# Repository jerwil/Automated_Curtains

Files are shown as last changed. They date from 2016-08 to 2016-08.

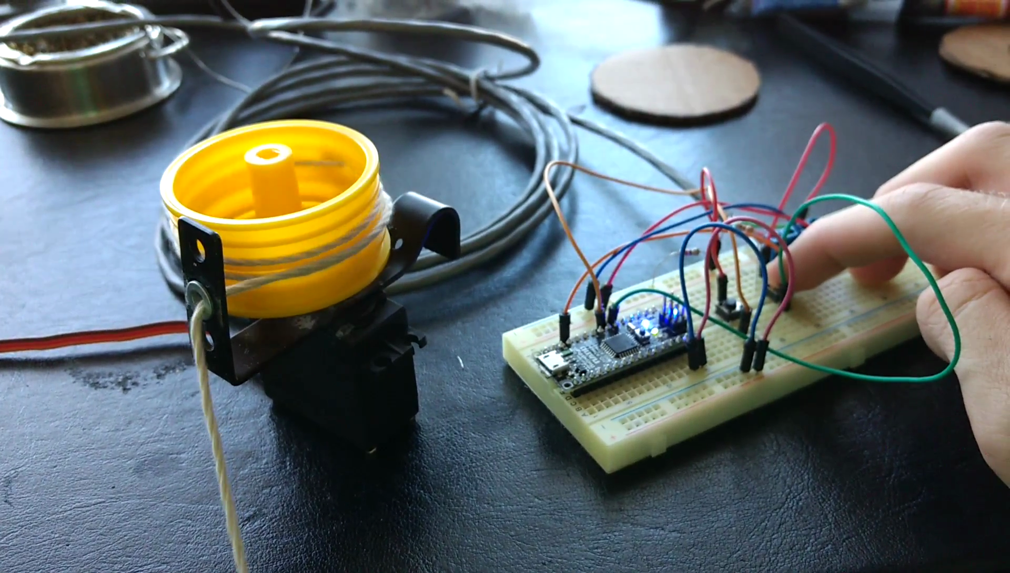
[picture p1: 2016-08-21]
Media/Progress Photos/Spool Test.png

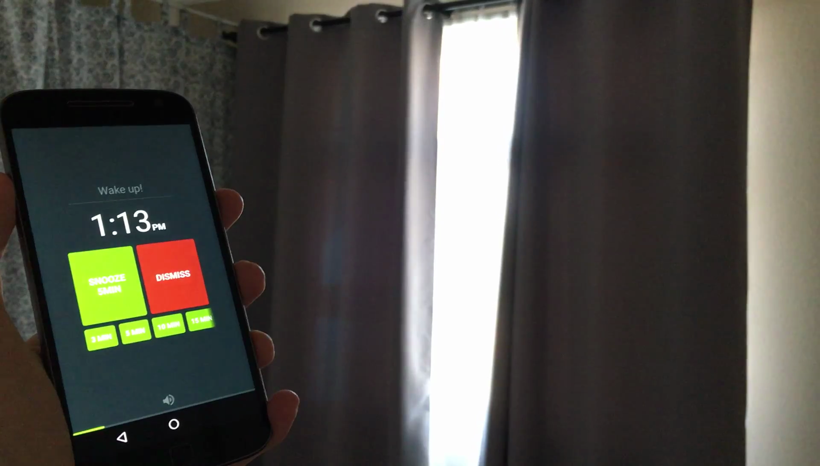
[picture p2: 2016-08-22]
Media/Curtain Opening.png

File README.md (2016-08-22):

# Alarm-Activated Automated Curtains
A system to automatically open the curtains when my cell phone alarm goes off

![] (https://github.com/jerwil/Automated_Curtains/raw/master/Media/Opening_GIF.gif)

##Features

* Uses inexpensive off-the-shelf parts to open curtain
* Seamlessly works with alarm app I already use
* Automatically retracts cord to allow curtains to be closed

##Architecture

![] (https://github.com/jerwil/Automated_Curtains/raw/master/Media/Comms%20Flowchart.png)

My alarm clock app, Sleep as Android, has the ability to interface with IFTTT. This is an awesome system that takes care of API calls for you and talks to hundreds of different services.

Sleep as Android >>> Adafruit IO

When the alarm goes off, Sleep as Android sends "alarm_alert_start" to a Maker channel feed. Using the [Sleep as Android documentation](http://sleep.urbandroid.org/documentation/integration/ifttt/), I created an [IFTTT recipe](https://ifttt.com/recipes/456351-when-my-sleep-as-android-alarm-goes-off-send-data-to-adafruit-io) that looks for this message, and writes a "1" to an Adafruit IO feed. When the alarm is disabled, "alarm_alert_dismiss" is sent, and a "0" is written to the data feed.

Adafruit IO >>> ESP8266

On the hardware side, I have an ESP8266 checking the Adafruit IO feed. I followed the basics of the [Adafruit guide](https://learn.adafruit.com/esp8266-temperature-slash-humidity-webserver/wiring) to get set up. When the feed returns a "1" the alarm is sounding, and the ESP8266 then lets the Arduino know it's time to open the curtain.

ESP8266 >>> Arduino

The connection between the ESP8266 and Arduino is very basic, just an on/off digital signal. When it's time to open the curtain, the ESP8266 writes a HIGH value on the digital line connecting the two microcontrollers.

Arduino Code

When the digital input is HIGH, the Arduino operates the servo to open the curtain, pauses, and then retracts the cord so that the curtain can be closed in the evening. The Arduino also has two buttons attached to it that allow the servo to be manually moved in either direction. These buttons also interrupt the automated open/close operation in case anything unexpected occurs.

The Arduino code also has a timeout (2 hours for now) during which no other alarm events will trigger the curtain opening. This avoids snoozing triggering the curtain multiple times in one morning.

## Wiring

![] (https://github.com/jerwil/Automated_Curtains/raw/master/Media/Breadboard%20Labeled.jpg)

See the included Fritzing diagram (.fzz file) for details. Thanks to [ydonnelly](https://github.com/ydonnelly/ESP8266_fritzing) for the ESP8266 Fritzing part!

![] (https://github.com/jerwil/Automated_Curtains/raw/master/Media/Breadboad.jpg)

## Hardware

![] (https://github.com/jerwil/Automated_Curtains/raw/master/Media/Servo%20Mounted.jpg)

The servo is mounted on the curtain rod, and has an old plastic wheel as a spool. As the servo turns, the spool reels in the string. The string is attached to the end of the curtain, so as it is pulled onto the spool, the curtain is dragged open.

![] (https://github.com/jerwil/Automated_Curtains/raw/master/Media/Progress%20Photos/Servo%20Washers.jpg)

The string has a bunch of washers along it such that there is tension when it unspools. The software will automatically unspool the string a few seconds after the curtain is dragged in so that the curtain can be later closed.

## Links

[Youtube video](https://www.youtube.com/watch?v=KcBI1g3s2vk)

[Hackaday.io Project Page](https://hackaday.io/project/13099-alarm-activated-curtains)

### License

<br /><span xmlns:dct="http://purl.org/dc/terms/" property="dct:title">Automated Curtains</span> by <a xmlns:cc="http://creativecommons.org/ns#" href="http://www.JeremyAdamWilson.com">Jeremy Wilson</a> is licensed under a <a rel="license" href="http://creativecommons.org/licenses/by-nc/4.0/">Creative Commons Attribution-NonCommercial 4.0 International License</a>.

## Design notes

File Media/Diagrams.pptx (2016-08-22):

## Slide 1

ESP8266

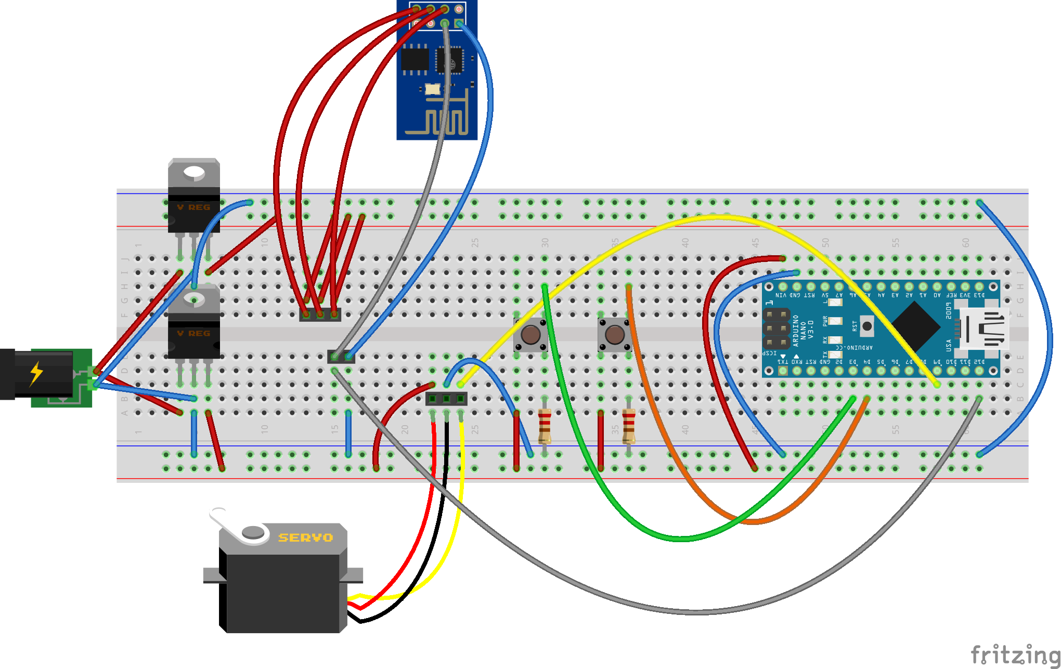
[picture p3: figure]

Manual open/close

3.3V

Arduino
Nano

5V

Alarm on/off signal

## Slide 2

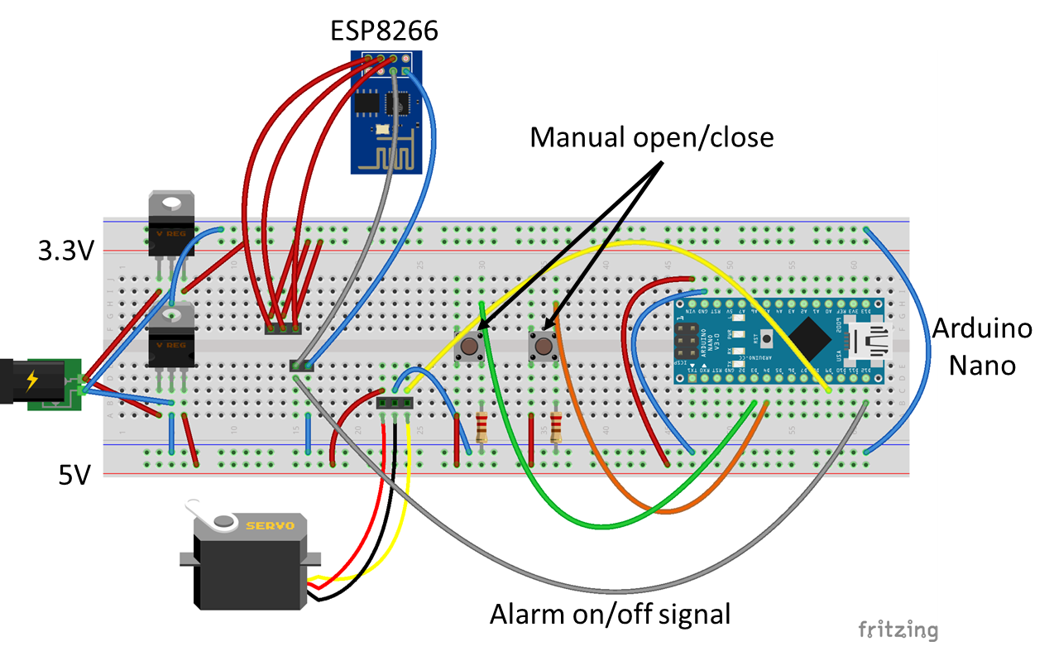
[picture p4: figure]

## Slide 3

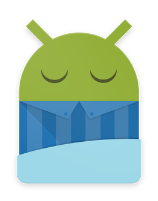
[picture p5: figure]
Screen Clipping

IFTTT Maker Channel

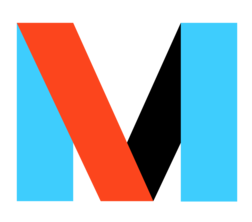
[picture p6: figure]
Screen Clipping

Adafruit IO

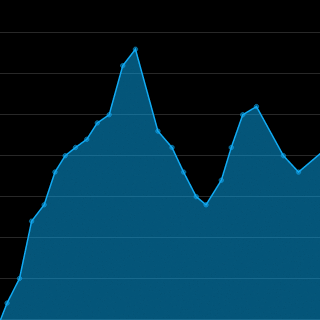
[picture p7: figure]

alarm_alert_start

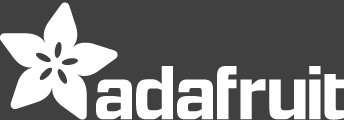
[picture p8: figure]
Adafruit Logo

Adafruit_IO_Client

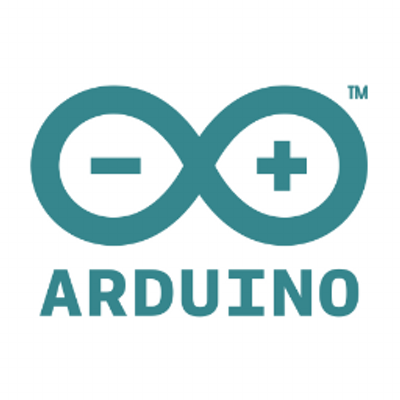
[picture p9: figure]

Servo

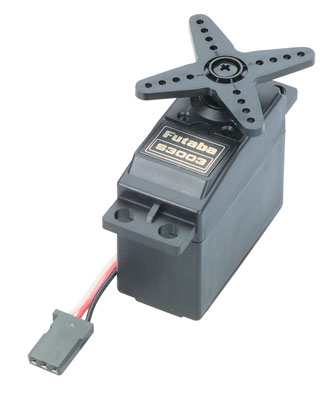
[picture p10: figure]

Nano

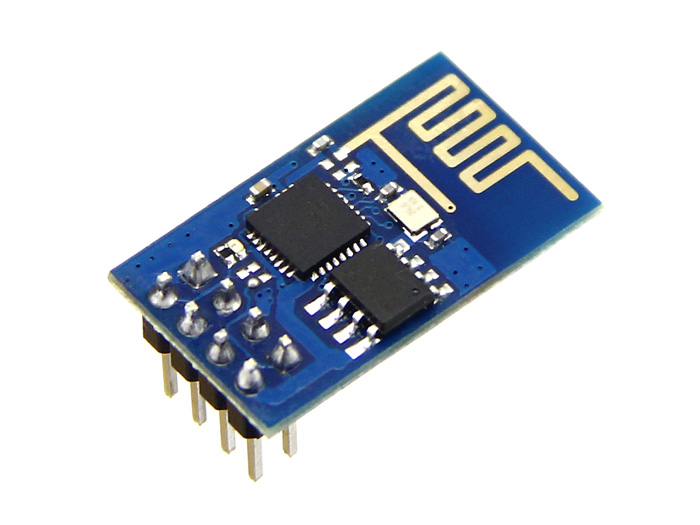
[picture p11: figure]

PWM

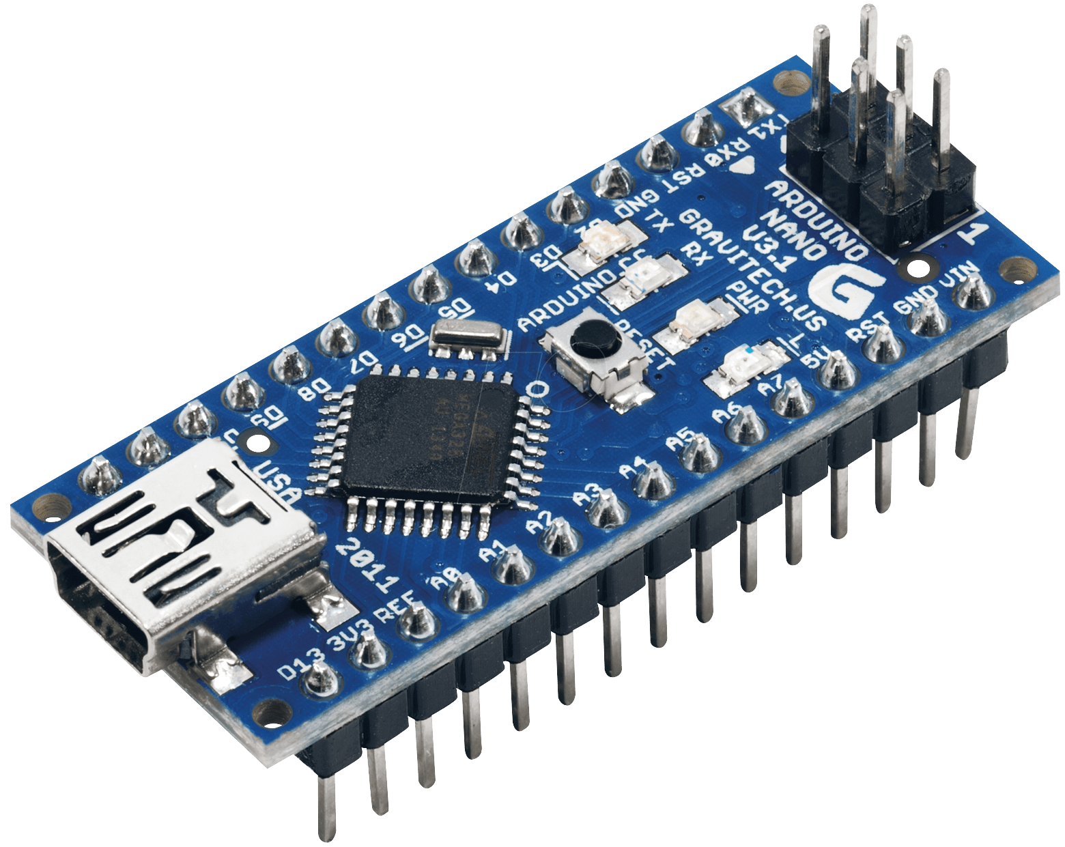
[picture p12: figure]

Digital HIGH

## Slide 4

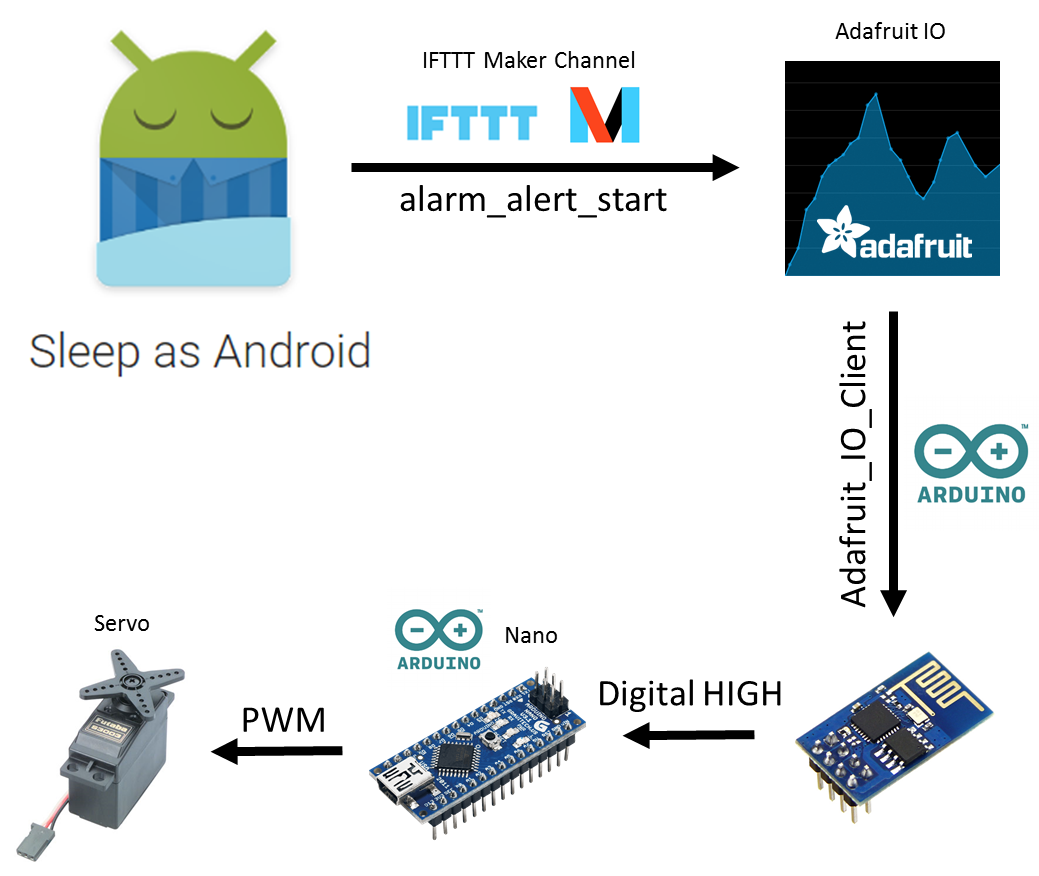
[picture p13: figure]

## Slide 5

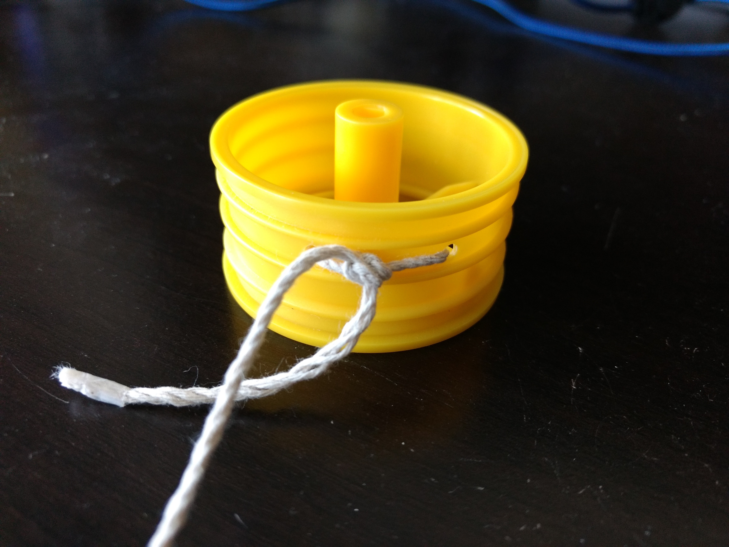
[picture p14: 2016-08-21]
Media/Progress Photos/Wheel as Spool.jpg

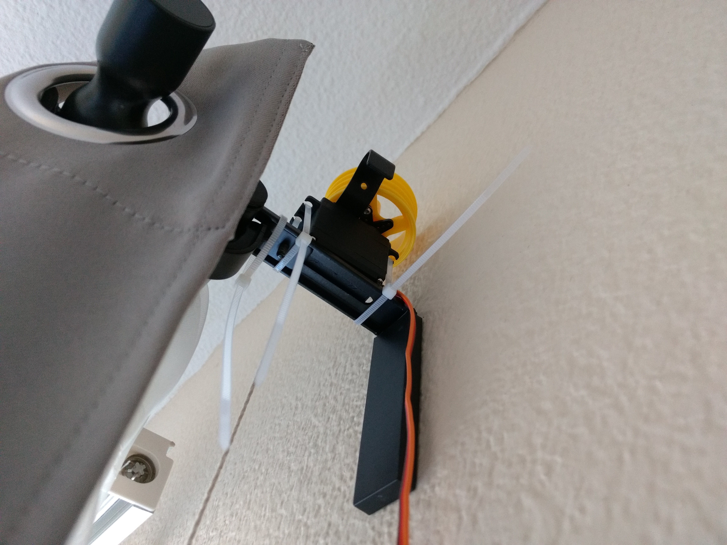
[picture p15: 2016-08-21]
Media/Progress Photos/Servo Mounted.jpg

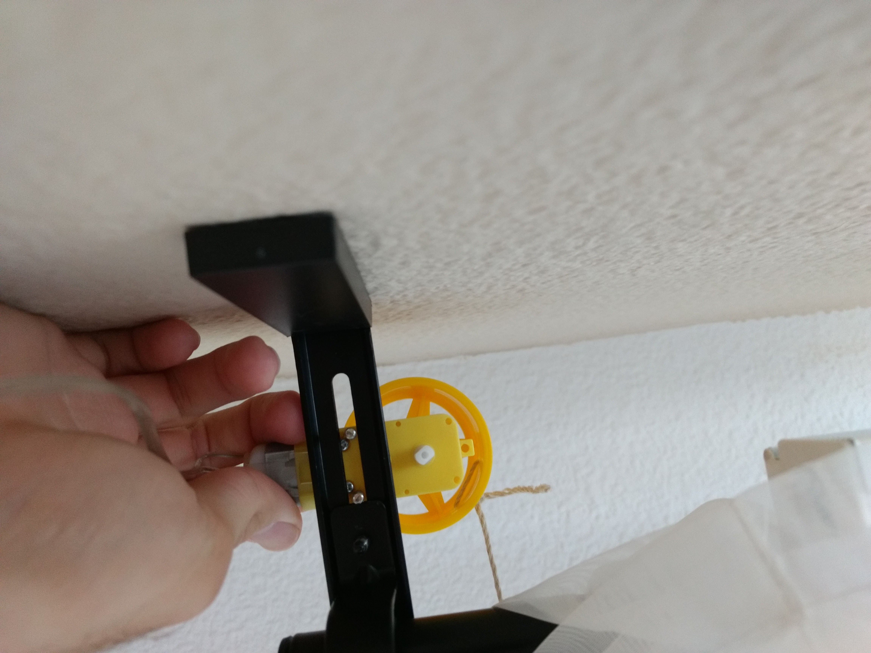
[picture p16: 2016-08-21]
Media/Progress Photos/DC Motor Mounted.jpg

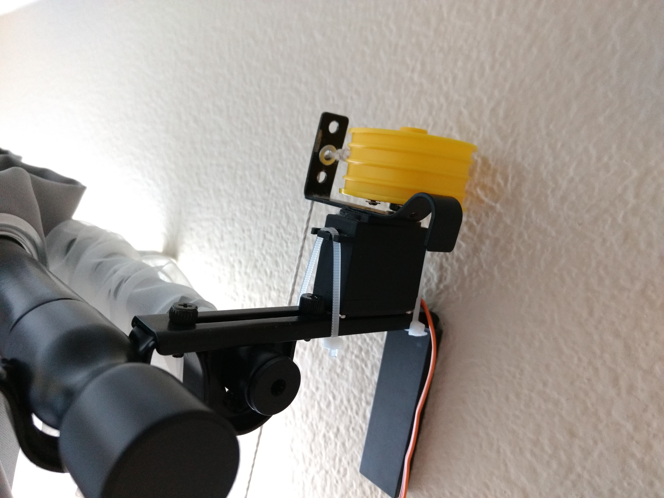
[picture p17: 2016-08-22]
Media/Servo Mounted.jpg

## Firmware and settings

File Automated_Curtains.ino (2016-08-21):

// Simple Motor Shield sketch

#include <Servo.h>

//Timekeeping variables:

double milis_timer[1] = {0}; // This is used to keep track of the timer used to tick for each milisecond
double second_timer[1] = {0}; // This is used to keep track of the timer used to tick for each second
double buffer_timer[1] = {0}; // This is used to keep track of the timer used to tick for each second
unsigned long currentTime;
word alarm_time_buffer = 7200; // If the alarm has gone off, wait until this amount of seconds have passed before it can be triggered again.
word alarm_time_passed = 7200; // The amount of seconds since the alarm was triggered
int pause_time = 10; // Time in seconds to pause between opening and closing
int pause_counter = 0; // Counter to track how long the system has paused for

double open_time = 9; // Time in seconds to open curtains
double close_time = 8.2; // Time in seconds to reset string

double motor_timer = 0;

// Button Variables

const int button1Pin = 3;     // the number of the pushbutton pin
const int button2Pin = 4;     // the number of the 2nd pushbutton pin
const int DIPin = 12;

int button1State = 0; 
int button2State = 0; 
int alarm_signal = 0;
int alarm_signal_timer = 0; // Timer and target are used to make sure that alarm signal is high for at least the target time to avoid noise
int alarm_signal_target = 2;



int motor_state = 0;

int curtain_state = 0; // Curtain is closed when state is 0, open when 1

char* mode = "idle";



// Declare classes for Servo connectors of the MotorShield.
Servo servo_1;
Servo servo_2;


void setup()
{
  Serial.begin(9600);
  Serial.println("Simple Motor Shield sketch");
  pinMode(button1Pin, INPUT);
  pinMode(button2Pin, INPUT);
  pinMode(DIPin, INPUT);

  // Use the default "Servo" library of Arduino.
  // Attach the pin number to the servo library.
  // This might also set the servo in the middle position.
  servo_1.attach(9);
  servo_2.attach(10);
}


void loop()
{
  
    button1State = digitalRead(button1Pin);
    button2State = digitalRead(button2Pin);
    alarm_signal = digitalRead(DIPin);
    
  if (tick(1000,buffer_timer) == 1){
    alarm_time_passed += 1;
    if (alarm_time_passed > 32000){alarm_time_passed = alarm_time_buffer + 1;} // Avoid overflow
    if (alarm_signal_timer >= alarm_signal_target && alarm_time_passed < alarm_time_buffer){
      Serial.println("Alarm is sounding, but it's too soon!");
      Serial.print(alarm_time_passed);
      Serial.print("/");
      Serial.print(alarm_time_buffer);
      Serial.println(" seconds since alarm went off");
    }
  }
  if (mode == "idle"){
    if (button1State == HIGH && button2State == LOW) {
      motor_state = 1;
      Serial.println("Forward!");
    }
    else if(button2State == HIGH && button1State == LOW){
      motor_state = -1;
      Serial.println("Backward!");
    }
    else{
      motor_state = 0;
    }
  if (tick(1000,second_timer) == 1){
  if (alarm_signal == 1) {    
      alarm_signal_timer +=1;
  }
  else {alarm_signal_timer = 0;}
  }
    if (alarm_signal_timer >= alarm_signal_target && alarm_time_passed > alarm_time_buffer){
    mode = "open";
    Serial.println("Open");
    alarm_signal_timer = 0;
    }
    
  }
  
  else if (mode == "open"){
    if (tick(100,milis_timer) == 1){
      motor_timer += .10;
      Serial.print("Motor timer: ");
      Serial.print(motor_timer);
      Serial.print("/");
      Serial.println(open_time);
    }
    if (motor_timer >= open_time){ 
      mode = "pause";
      motor_timer = 0;
      Serial.println("Pausing");
    }
    else if (button1State == HIGH || button2State == HIGH){ // Allow user to interrupt automatic opening
      mode = "idle";
      motor_timer = 0;
      Serial.println("interrupted by user");
    }
    motor_state = 1;
    pause_counter = 0;
    alarm_time_passed = 0;
  }
  
  else if (mode == "pause"){
    motor_state = 0;
    if (tick(1000,milis_timer) == 1){
      pause_counter += 1;
      Serial.print("Pause timer: ");
      Serial.print(pause_counter);
      Serial.print("/");
      Serial.println(pause_time);
    }
    if (pause_counter >= pause_time){
      mode = "close";
      pause_counter = 0;
    }
  }
  
  else if (mode == "close"){
    if (tick(100,milis_timer) == 1){
      motor_timer += .10;
      Serial.print("Motor timer: ");
      Serial.print(motor_timer);
      Serial.print("/");
      Serial.println(close_time);
    }
    if (motor_timer >= close_time || button1State == HIGH || button2State == HIGH){
      mode = "idle";
      motor_timer = 0;
      Serial.println("Idle State");
    }
    motor_state = -1;
  }
  
  
  // Write to motor
  if (motor_state == 1){
    servo_1.write(180);
  }
  else if (motor_state == -1){
    servo_1.write(0);
  }
  else if (motor_state == 0){
    servo_1.write(90);
  }
  else{
    servo_1.write(90);  
  }

}

int tick(int delay, double timekeeper[1]){
currentTime = millis();
if(currentTime >= (timekeeper[0] + delay)){
  timekeeper[0] = currentTime;
  return 1;
  }
else {return 0;}
}

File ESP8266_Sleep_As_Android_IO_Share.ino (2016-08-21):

// Adafruit IO REST API access with ESP8266
//
// For use with ESP8266 Arduino from:
//   https://github.com/esp8266/Arduino
//
// Works great with ESP8266 modules like the Adafruit Huzzah ESP:
//  ----> https://www.adafruit.com/product/2471
//
// Written by Tony DiCola for Adafruit Industries.  
// MIT license, all text above must be included in any redistribution.
#include <ESP8266WiFi.h>
#include "Adafruit_IO_Client.h"

const int DOPin = 2;     // Digital output to Arduino to tell it to open/close


// Configure WiFi access point details.
#define WLAN_SSID  "XXXXXXXX"
#define WLAN_PASS  "XXXXXXXXX"

// Configure Adafruit IO access.
#define AIO_KEY    "XXXXXXXXXXXXXXXXXXXXXXXXXXXXXXXXX"


// Create an ESP8266 WiFiClient class to connect to the AIO server.
WiFiClient client;

// Create an Adafruit IO Client instance.  Notice that this needs to take a
// WiFiClient object as the first parameter, and as the second parameter a
// default Adafruit IO key to use when accessing feeds (however each feed can
// override this default key value if required, see further below).
Adafruit_IO_Client aio = Adafruit_IO_Client(client, AIO_KEY);

// Finally create instances of Adafruit_IO_Feed objects, one per feed.  Do this
// by calling the getFeed function on the Adafruit_IO_FONA object and passing
// it at least the name of the feed, and optionally a specific AIO key to use
// when accessing the feed (the default is to use the key set on the
// Adafruit_IO_Client class).
Adafruit_IO_Feed alarmfeed = aio.getFeed("alarmfeed");

// Alternatively to access a feed with a specific key:
//Adafruit_IO_Feed testFeed = aio.getFeed("esptestfeed", "...esptestfeed key...");

// Global state to increment a number and send it to the feed.
unsigned int count = 0;

void setup() {
  // Setup serial port access.
  Serial.begin(115200);
  delay(10);
  Serial.println(); Serial.println();
  Serial.println(F("Adafruit IO ESP8266 test!"));
pinMode(DOPin, OUTPUT);
digitalWrite(DOPin,LOW);

  // Connect to WiFi access point.
  Serial.print("Connecting to ");
  Serial.println(WLAN_SSID);

  WiFi.begin(WLAN_SSID, WLAN_PASS);
  while (WiFi.status() != WL_CONNECTED) {
    delay(500);
    Serial.print(".");
  }
  Serial.println();

  Serial.println("WiFi connected");  
  Serial.println("IP address: "); Serial.println(WiFi.localIP());
  
  // Initialize the Adafruit IO client class (not strictly necessary with the
  // client class, but good practice).
  aio.begin();

  Serial.println(F("Ready!"));
  
}

void loop() {

  // To read the latest feed value call the receive function on the feed.
  // The returned object will be a FeedData instance and you can check if it's
  // valid (i.e. was successfully read) by calling isValid(), and then get the
  // value either as a text value, or converted to an int, float, etc.
  FeedData latest = alarmfeed.receive();
  if (latest.isValid()) {
    Serial.print(F("Received value from feed: ")); Serial.println(latest);
    // By default the received feed data item has a string value, however you
    // can use the following functions to attempt to convert it to a numeric
    // value like an int or float.  Each function returns a boolean that indicates
    // if the conversion succeeded, and takes as a parameter by reference the
    // output value.
int i;
   if (latest.intValue(&i)) {
     Serial.print(F("Value as an int: ")); Serial.println(i, DEC);
    }
    // Other functions that you can use include:
    //  latest.uintValue() (unsigned int)
    //  latest.longValue() (long)
    //  latest.ulongValue() (unsigned long)
    //  latest.floatValue() (float)
    //  latest.doubleValue() (double)
  if (i == 1){
    digitalWrite(DOPin,HIGH);
    Serial.println("Alarm on!");
    }
  else{
    digitalWrite(DOPin,LOW);
  }
  }
  else {
    Serial.print(F("Failed to receive the latest feed value!"));
    digitalWrite(DOPin,LOW);
  }

  // Now wait 10 more seconds and repeat.
  Serial.println(F("Waiting 10 seconds and then writing a new feed value."));
  delay(1000);
}

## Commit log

2016-08-20 Initial commit - basic two-button operation
    Simple code to rotate a servo forward and backward with two buttons.
    Used to automatically open a curtain
2016-08-20 Added timed closing and opening
    Now use button to toggle between opening and closing. Can press any
    button to interrupt. Will be used to set open/close times
2016-08-21 Calibrated open/closed times. Added media
2016-08-21 Arduino responds to digital input to open
    And added schematic. Added alarm buffer so that alarm does not continue
    to cause curtain to open and close. Arduino awaits digital signal from
    ESP8266 for alarm event
    [Automated_Curtains_Schematic.fzz]
2016-08-22 Completed schematic, added diagrams
    [Automated_Curtains_Schematic.fzz]
